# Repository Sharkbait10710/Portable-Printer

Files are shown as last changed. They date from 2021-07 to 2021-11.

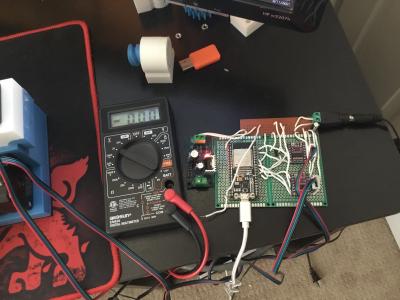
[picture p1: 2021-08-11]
Portable Printer Circuit Board.jpg

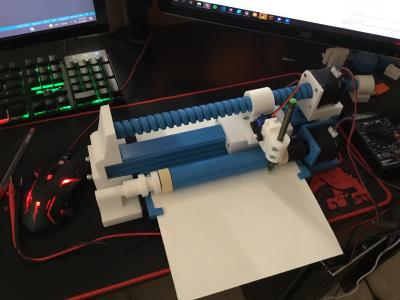
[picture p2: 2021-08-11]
Portable Printer.jpg

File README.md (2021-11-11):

# Portable Printer

The goal of this project is to create a robust printer that is lightweight and rigid in structure, capable of sketching images on 8.5 x 11 printer paper with relatively high accuracy by using a pen and resume printing capability, and has user-friendly UI software that can send virtual images to printer in real-time (image is still in progress, but would like to be drawn immediately) or by completion (image is complete and ready to print).

Access CAD design -> CAD files and open Chassis Assembly.SLDASM to view model.
All CAD, electronics, and programming were done by Dang Le.

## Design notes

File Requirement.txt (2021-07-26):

1) Structural rigid and relatively lightweight for easy transportation
    wires are simple and easy to store
    electronics are well protected and safety concealed to protect users and printer

2) Uses a pen to draw on printer paper 
    printer must be minimum 8.5 x 11 in to accomodate printer paper
    sketched drawing should be relatively accurate to user's sketched
    consistent prints
    print speed should be reasonable
    if power is lost, printer can resume printing

3) Incorporates a user-friendly UI that can accept user drawings and prints them via Portable printer
    UI should be IOS friendly 
    should be able to print real-time(image is still in progress, but would like to be drawn immediately) and by completion (image is complete and ready to print)

Possible improvements:
    as cheap as possible with maximum quality
    as fast as possible without compromising sketch quality or damage to parts
    as compact as possible

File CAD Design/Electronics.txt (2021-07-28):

Since there are two stepper motors, two DRV8255 drivers will be needed to control them
Since self-sensing is one of the capabilities of this project, the project will need two tactile sensors
        one being the endstop switch (for leadscrew motion)
        not sure if enstop would be able to detect paper though. Better than using other sensors due to price
            initially thinking of VCSEL (vertical cavity surface emitting laser), like SparkFun VL53L1X, but it
            was too expensive
        maybe use a proxmity sensor for paper sensor
        try infrared diode led IR emission and reciever
        *****USE https://www.amazon.com/Gikfun-Infrared-Emitter-Receiver-Arduino/dp/B01HGIQ8NG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
        AND https://www.youtube.com/watch?v=_mOF1JXo1DU TO CREATE OWN PROXIMITY SENSOR*****
    to detect the location of the paper and the pen
A 12V power supply is needed to power the motor drivers and a step down /  6-7 power supply is needed to
    power the ESP32 
Use PCB for circuit board
    I'm gonna try Altium CircuitMaker (software to make Gerber file) and JLCPCB (manufacturer)

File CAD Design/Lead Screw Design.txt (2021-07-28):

The lead screw cannot have a lead that is too small because the stepper motor must turn faster to make the nut carrier 
move faster. However, doing this requires sending pulses much quicker to the stepper motor, which generates more rapidly
changing currents. This in turn causes the stator windings to create stronger magnetic fields, thus more friction, and less
torque.

An increase in rotational friction due to stronger magnetic fields which are in turn due to high pulse per second (PPS) can
cause the nut mount to vibrate during prints, which would decrease print quality. Therefore, a cap on linear speed should be 
specify.

Since linear speed is equivalent to the rotational speed of the stepper motor times the lead per rotation, a larger lead 
will increase linear speed. Furthermore, lower rotational speeds are required to travel the same distance compared to leads that are 
smaller. However, this would require microstepping for more accurate positioning of the nut carrier, which would decrease the torque
output by about 30%.

Longer lead will significantly lower print time and reduce friction due to stronger magnetic fields (hence increase torque output),
but will decrease gear ratio and overall accuracy. What a short lead can due is increase precision and significantly increase torque
output, but there is a significantly trade off for speed.

So, for quick prints, longer leads are more effective, but for precise prints, short leads are better.
    for high precision, use short leads and use lower speeds.

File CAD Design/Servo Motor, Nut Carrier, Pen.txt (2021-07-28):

The nut carrier will be placed on a linear guide and is attachable by bolts and nuts. This will allow replacement of leads
which will help evaluating leads and determine which lead produces the best quality and print time.

The servo motor will be attached onto the nut carrier via bolts and nuts for easy disassemble and placed on its side
such that the shaft is pointing long at the lead screw axis. 

The servo motor will use a quick return mechanism to lift and lower the pen on the paper. A servo motor is a good choice
to do this because it provides strong output torque to prevent the pen from moving up or down, thus reducing vibrations
and improving print quality. 

The pen will be mounted on a pen mount that will securely hold the pen and prevent the pen from slipping. A pen 
coupling would be needed to do this and should be able to tighten and untighten for easy disassemble. The pen mount will
be able to move up and down and its position will be controlled via the quick return mechanism. The pen mount shouldn't 
be too heavy and should not cause the pen to lean.

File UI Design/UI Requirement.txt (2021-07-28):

requirement
    1) Should have immediate mode for user to choose
        immediate will have an idle timer that starts when user no longer drawing
        when idle timer timeouts, printer should get drawing data from user and start printing
    2) Should have complete mode for user to choose
        when user confirms that drawing is completed, printer will take the data and print out the drawing
        should have an abort option to abort drawing if user chooses to do should
    3) Should have a resume feature
        software should check if printer is still running and/or completed drawing
        if not completed, software should log the print job's progress so that when printer is online again, printing can resume
        user should be notified that printer has not finished printjob and that printer has been turned off
    4) User drawing should be logged 
    5) User should be able to draw on UI and drawing data can be exported to printer
        *ideal if UI can reduce print time as much as possible, but maximize print quality
    6) Closed boundaries in drawing should be shaded or any other method that is NOT filled in
    7) Software will notify user when drawing is completed
    8) Software is IOS compatible

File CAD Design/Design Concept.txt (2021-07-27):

Major Parts

    Chassis
        Consist of NEMA 17 stepper motor, lead screw, and nut carrier that moves pen mount
        houses electronics
        paper passes through Chassis
        *ball bearings to house lead screw
        *rod shaft to support nut carrier
        *use rectangular structure embedded under lead screw

    Pen Mount
        actached to nut carrier and moves as NEMA 17 rotates its shaft
        tightly attached to pen
        uses servo motor to lift and depress pen
        can lift pen easily and quickly
        mounted on wheels for reduction of friction
        use quick-draw (not correct name) mechanism to lift pen during non-drawing time
        sensor to help locate pen

    Roller
        accepts paper and consistent pushes paper under pen mount   
        paper distance inside chassis is consistently and accurately controlled
        controlled using spur gear and stepper motor
        feeds paper into chassism where pen will draw on paper
        should be able to push paper in and pull paper out
        sensor to detect paper

    Paper Dispenser
        straightens paper and minimizes curls in the paper
        should keep paper down as pen is moving back and forth

    electronics
        use PCB board and attach to all motors (stepper and servo), sensor, and microncontroller
        microncontroller is esp32 for internet capability
        12V power supply 
        DRV8255 motor driver
        *need 5-8ish power supply to power esp32

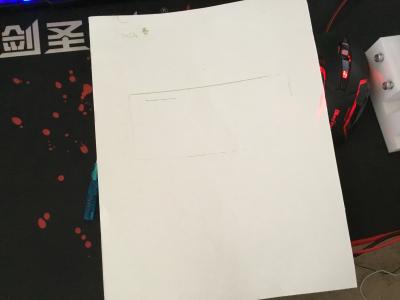
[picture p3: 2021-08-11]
Sketch of Rectangle.jpg

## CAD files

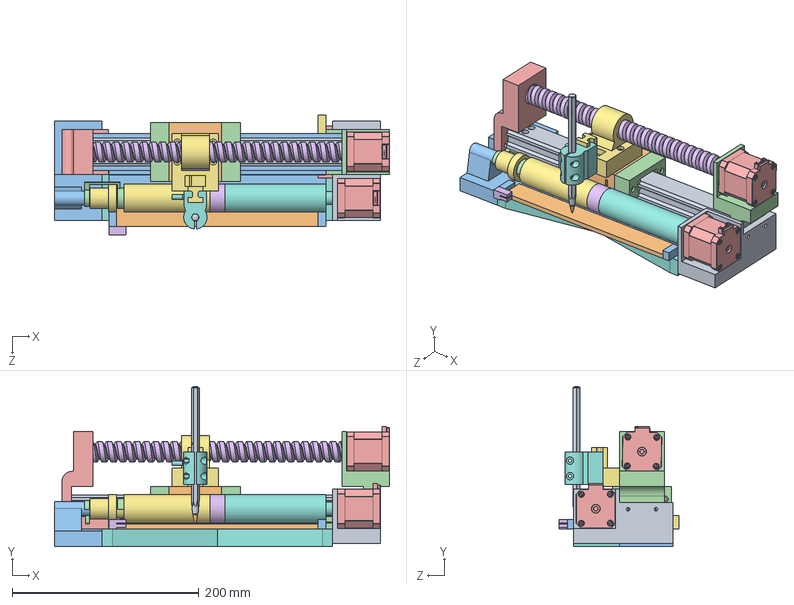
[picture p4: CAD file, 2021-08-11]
CAD Design/CAD Files/Chassis Assembly.SLDASM
358.8 x 171.4 x 128.7 mm
Linear Guide Rail
Linear Guide Carrier
7by3 inch Ball x 104
Linear Guide Cap x 2
Nema 17 Stepper Motor x 2
lead screw
nut carrier
Bic Pen Coupling
bic_pen
inner part
Chassis
chassis right wing
chassis left wing
paper feed roll
roller
roller 2
chassis right foot
paper plane
chassis left foot
paper detector
paper feed chassis part
paper side feeds
paper side back
X Brace

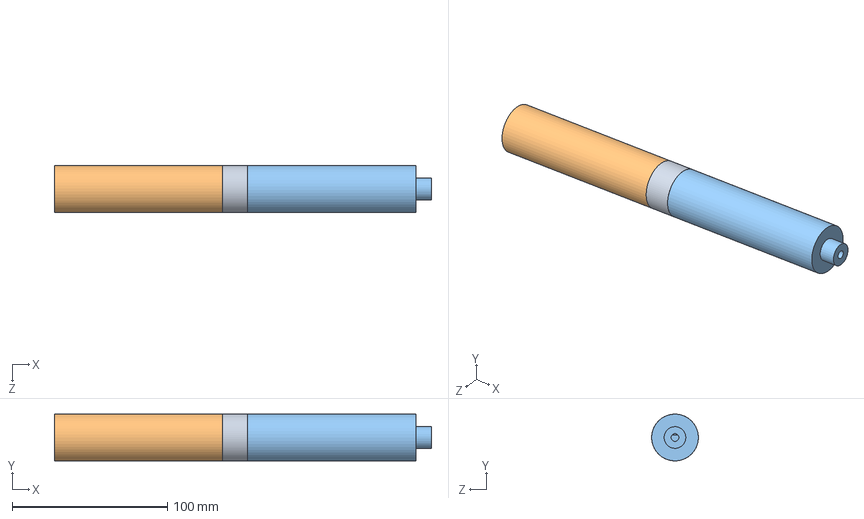
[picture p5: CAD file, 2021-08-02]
CAD Design/CAD Files/roller.SLDASM
243.0 x 30.1 x 30.2 mm
paper feed roll
roller
roller 2

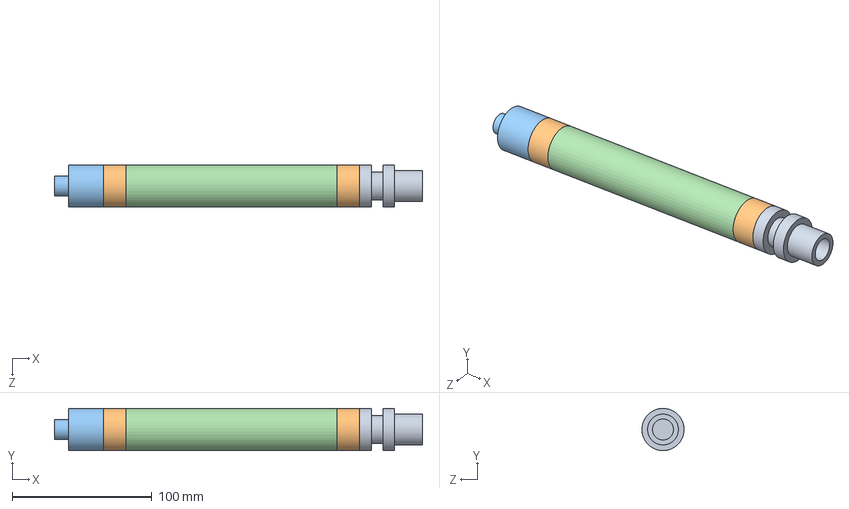
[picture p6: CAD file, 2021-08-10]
CAD Design/CAD Files/Improvements/roller improv.SLDASM
263.0 x 30.2 x 30.2 mm
roller improv
paper feed roll x 2
roller 2 improv
roller improv 3

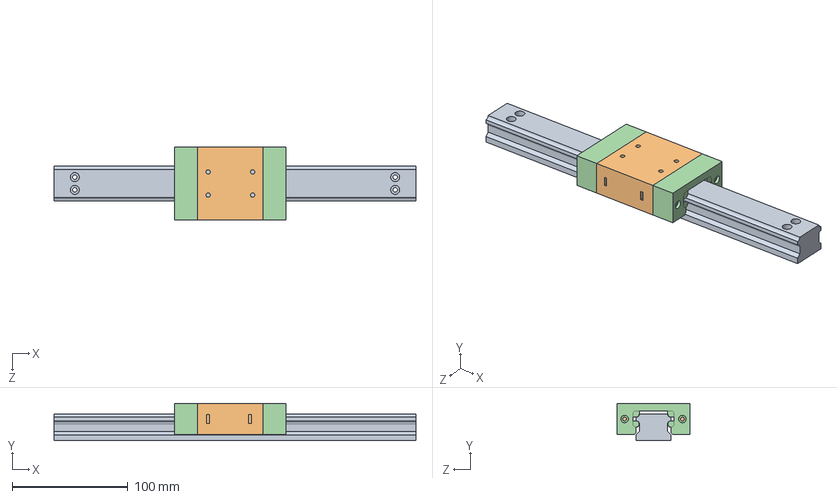
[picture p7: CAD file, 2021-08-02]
CAD Design/CAD Files/linear guide.SLDASM
313.0 x 32.1 x 63.5 mm
Linear Guide Rail
Linear Guide Carrier
7by3 inch Ball x 104
Linear Guide Cap x 2

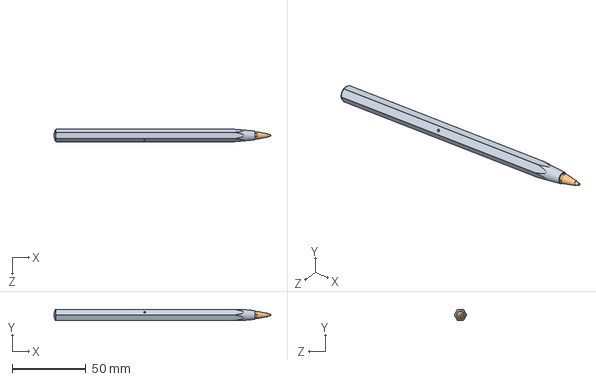
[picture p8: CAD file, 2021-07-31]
CAD Design/CAD Files/Bic Pen.SLDASM
147.1 x 7.40 x 8.50 mm
bic_pen
inner part

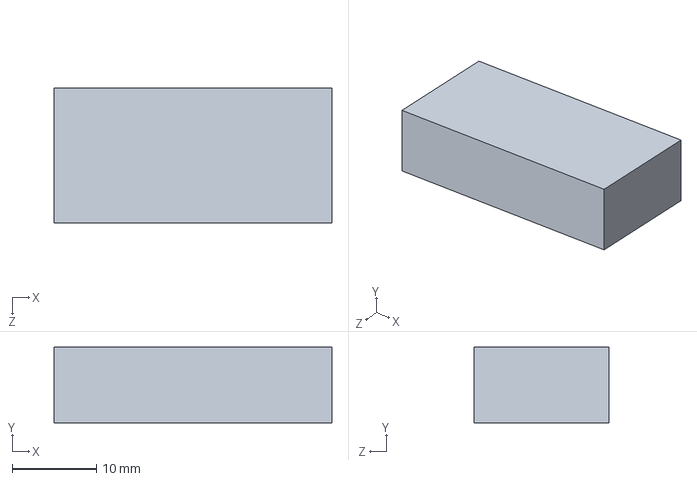
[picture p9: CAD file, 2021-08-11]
CAD Design/CAD Files/Improvements/chassis right wing support 3.SLDPRT
33.0 x 9.00 x 16.1 mm

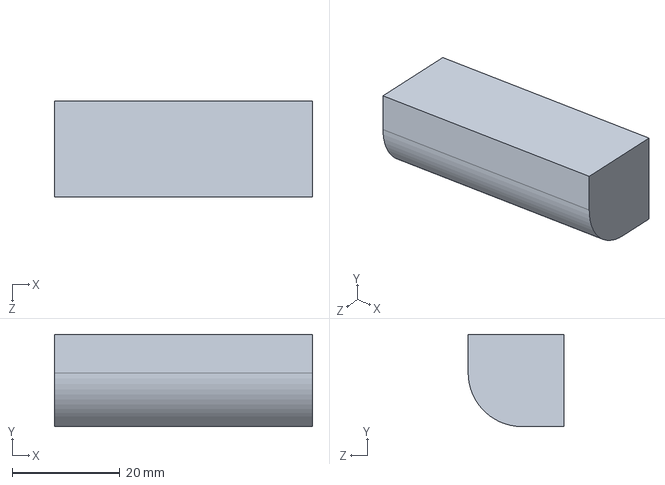
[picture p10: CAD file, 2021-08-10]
CAD Design/CAD Files/Print Folder/chassis right wing support P.SLDPRT
48.0 x 17.1 x 17.8 mm

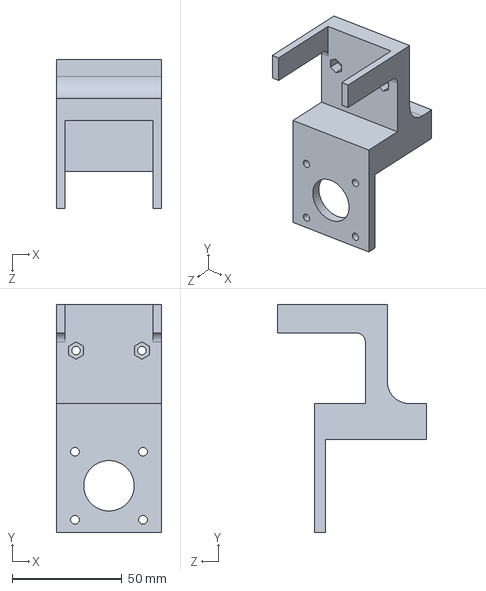
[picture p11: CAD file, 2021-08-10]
CAD Design/CAD Files/chassis right wing.SLDPRT
48.0 x 103.9 x 67.8 mm

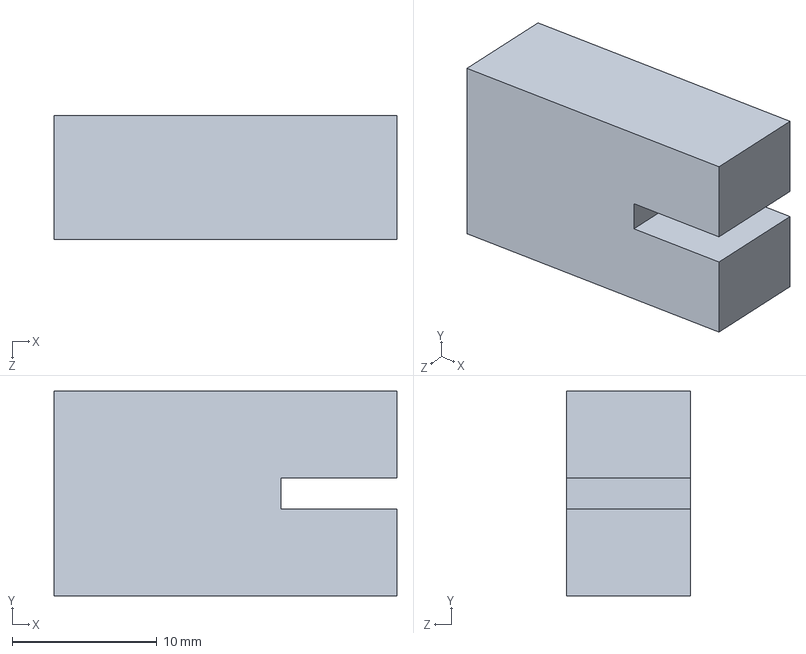
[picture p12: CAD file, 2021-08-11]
CAD Design/CAD Files/Improvements/paper side back 2.SLDPRT
23.7 x 14.2 x 8.55 mm

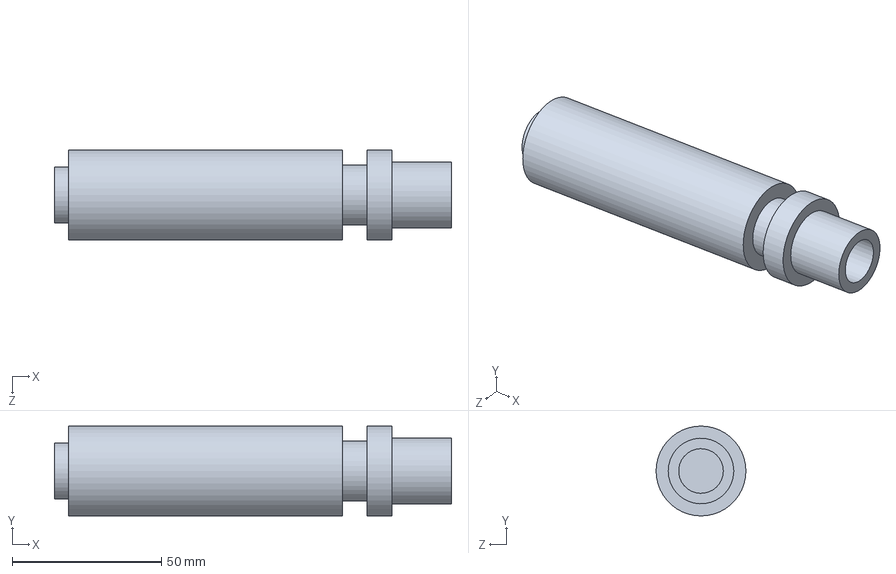
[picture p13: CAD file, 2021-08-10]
CAD Design/CAD Files/Print Folder/roller P.SLDPRT
133.2 x 30.2 x 30.2 mm

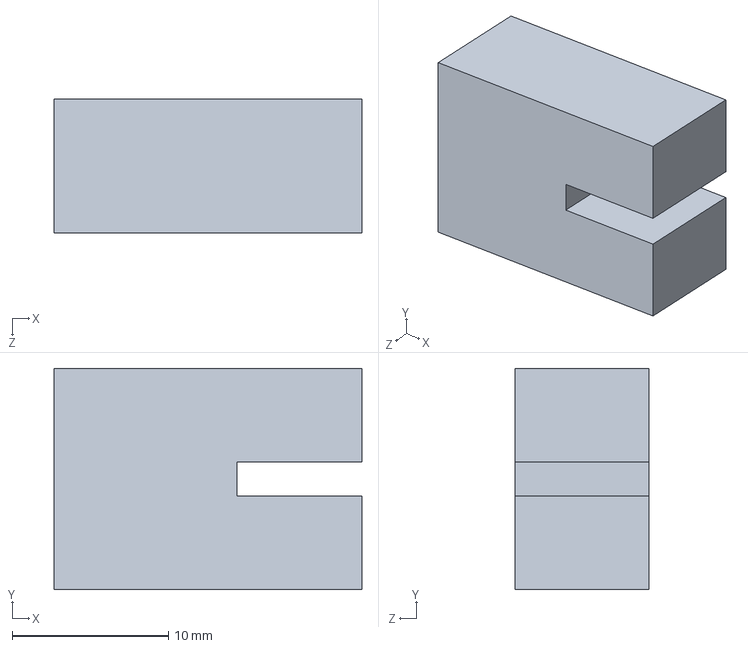
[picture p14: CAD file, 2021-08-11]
CAD Design/CAD Files/Improvements/paper side back.SLDPRT
19.7 x 14.2 x 8.55 mm

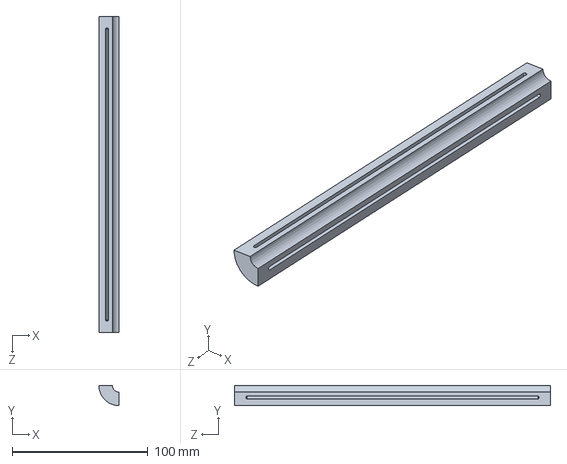
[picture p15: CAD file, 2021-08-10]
CAD Design/CAD Files/paper slide.SLDPRT
15.0 x 15.0 x 232.5 mm

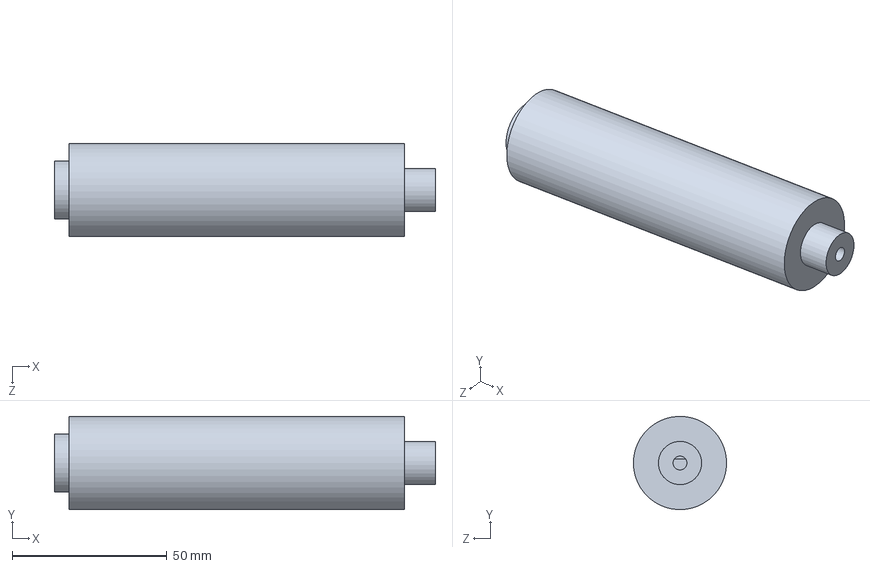
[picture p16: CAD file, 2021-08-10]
CAD Design/CAD Files/Print Folder/roller 2 P.SLDPRT
123.2 x 30.1 x 30.2 mm

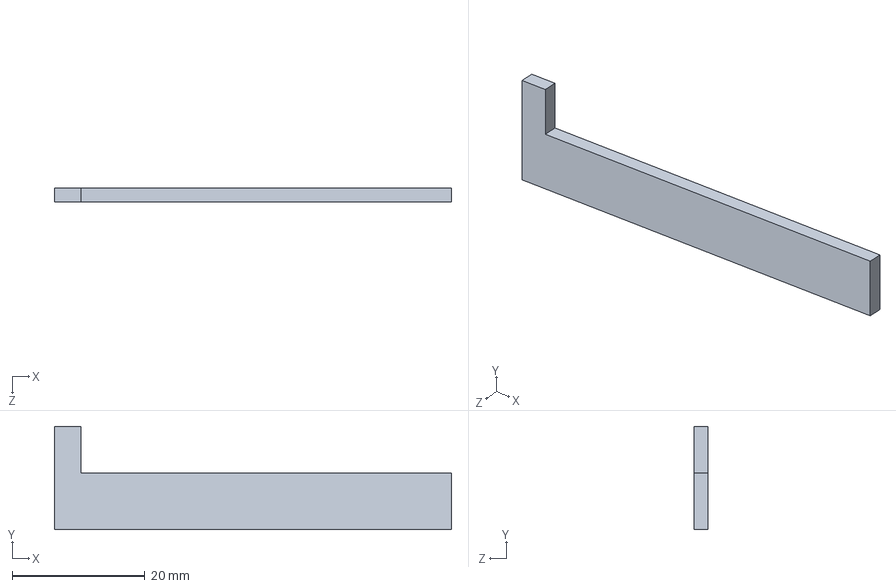
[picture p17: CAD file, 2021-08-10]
CAD Design/CAD Files/Improvements/paper feed chassis part 3.SLDPRT
59.9 x 15.5 x 2.15 mm

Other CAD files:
CAD Design/CAD Files/Print Folder/chassis right wing support 2 P.SLDPRT
CAD Design/CAD Files/Chassis.SLDPRT
CAD Design/CAD Files/Improvements/chassis right wing support 2.SLDPRT
CAD Design/CAD Files/Print Folder/Chassis P.SLDPRT
CAD Design/CAD Files/7by3 inch Ball.SLDPRT
CAD Design/CAD Files/Bic Pen Coupling.SLDPRT
CAD Design/CAD Files/Improvements/X Brace 2.SLDPRT
CAD Design/CAD Files/Improvements/X Brace.SLDPRT
CAD Design/CAD Files/Improvements/chassis left foot mod.SLDPRT
CAD Design/CAD Files/Improvements/chassis left foot no rod support.SLDPRT
CAD Design/CAD Files/Improvements/chassis left foot only rod support.SLDPRT
CAD Design/CAD Files/Improvements/chassis right wing support.SLDPRT
CAD Design/CAD Files/Improvements/paper feed chassis part 2.SLDPRT
CAD Design/CAD Files/Improvements/paper feed chassis part.SLDPRT
CAD Design/CAD Files/Improvements/paper side feeds.SLDPRT
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

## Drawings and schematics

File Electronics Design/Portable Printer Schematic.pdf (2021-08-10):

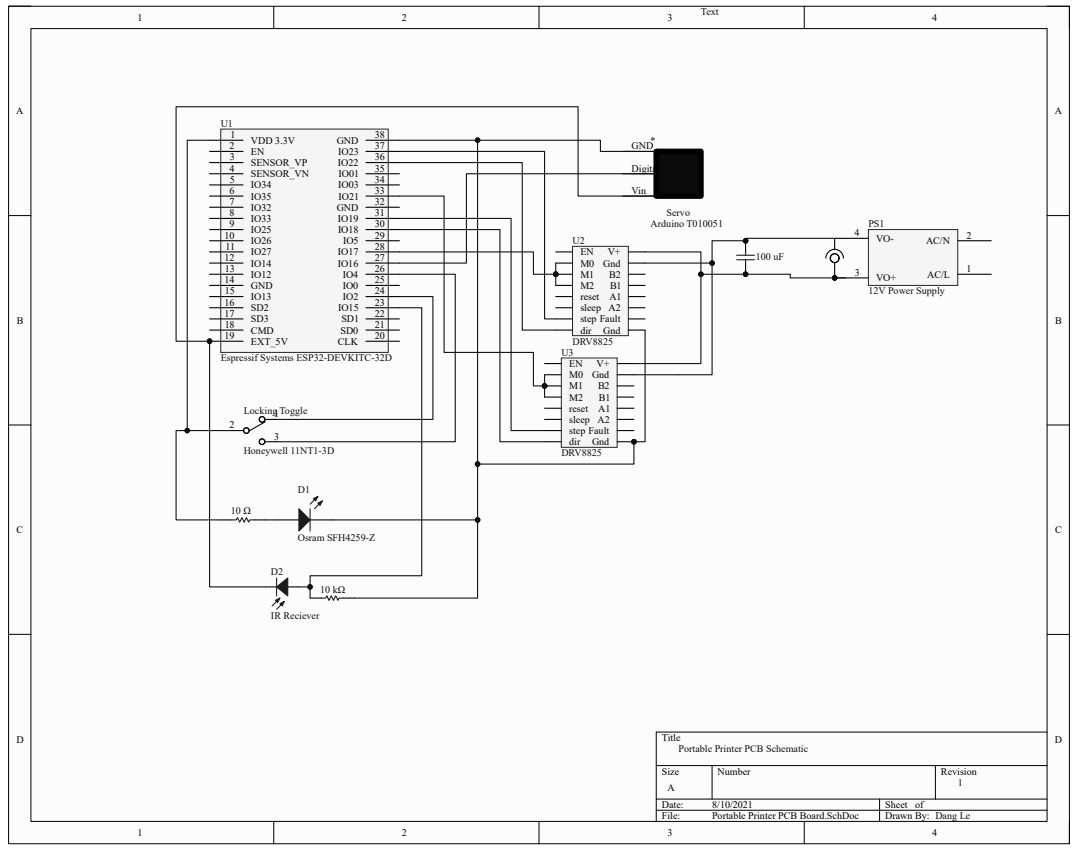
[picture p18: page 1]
VDD 3.3V 1 EN 2 SENSOR_VP 3 SENSOR_VN 4 IO34 5 IO35 6 IO32 7 IO33 8 IO25 9 IO26 10 IO27 11 IO14 12 IO12 13 GND 14 IO13 15 SD2 16 SD3 17 CMD 18; EXT_5V 19; CLK; 31 GND; 37 GND; Locking Toggle; Honeywell 11NT1-3D; Osram SFH4259-Z; GND; Digital; Vin; Servo; Arduino T010051; EN M0 M1 M2 reset sleep step dir Gnd; Fault; Gnd; DRV8825; 12V Power Supply; Text; IR Reciever

Espressif Systems ESP32-DEVKITC-32D

Title
Portable Printer PCB Schematic

Size A | Number | Revision 1

Date: 8/10/2021 | Sheet of
File: Portable Printer PCB Board.SchDoc | Drawn By: Dang Le

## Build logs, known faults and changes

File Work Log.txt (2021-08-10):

2021-07-26 13:45:13
    {
        Created Git Repository
        Laid out general idea of project in README.md
    }

2021-07-26 14:11:13
    {
        watched youtube.com/watch?v=6BkYcqe8Vmo "How to convert rotational motion into linear motion | Lemurian Designs"
            and discovered the lead screw assembly
    }

2021-07-26 14:44:10
    {
        watched https://www.youtube.com/watch?v=BstZUC4tcOA "Power Screws - Torque to Force Relationships in Just Over 10 Minutes!"
            and learned that one full rotation, for single thread screw, will advance output load by lead (l)
    }

2021-07-26 15:00:18
    {
        Wrote requirement for project
    }

2021-07-26 15:12:06
    {
        Created Design folder, which would house the SW files, and currently contains the general design idea text file
    }

2021-07-27 07:35:52 
    {
        Continued working on Design Concept. Have good idea of CAD design now
    }

2021-07-27 07:45:39
    {
        Laid out requirement for UI
    }

2021-07-27 17:02:59 
    {
        Researched GUI design and how to use CSS. Found Bootstrap and plan to implement it.
        Learned about Ultralight which "enables you to build your application's GUI with web pages and C/C++"
    }

2021-07-27 19:19:34
    {
        Learned about linear guide from https://youtu.be/XZXadrjIm_4 and discovered cad file at https://www.thingiverse.com/thing:2847294
    }

2021-07-27 19:59:05
    {
        Instead of using shafts for linear bearings, using linear guide is better since it saves more space. The thingiverse link would
        serve as a guide. Need balls though, this link looks good https://www.amazon.com/500Pcs-Assorted-Loose-Bicycle-Bearing/dp/B085T3BT92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
    }

2021-07-28 06:20:56 
    {
        Learned how stepper motors work from https://www.youtube.com/watch?v=TWMai3oirnM "Stepper Motor - How It Works." 
        Pulses are sent to stepper motor which create varying magnetic fields to turn a permanent magnet (or something similar) to in order to change its rotational position.
    }

2021-07-28 06:37:45
    {
        Learned even more about stepper motor. A single digital pulse moves a single step by energizing coil (I think running current briefly generates a magnetic field in 
        one coil, but when current begins to stop a magnetic field in the opposite direction is generated). Microstepping is also possible.
    }

2021-07-28 06:44:43
    {
        I learned more about stepper motors and learned that there are 2 coils inside a stepper motor and each coil is energized alternatively in order to generate
        magnetic fields in the same direction to rotate the shaft.
        Check out https://www.youtube.com/watch?v=09Mpkjcr0bo "How Stepper Motors Work - Electric motor"
    }

2021-07-28 07:19:03
    {
        I worked on the lead screw design. I will wait for the paper feed roller design after I recieve the rollers today. I'm not completely sure how the roller will
        effective feed paper without causing curlings. I'm also not sure how to prevent the paper from curling in general as it enters the chassis. My questions are 
        "Does the pen cause the paper to curl?" "Will the paper need to be fed into a narrow slit to hold the paper down and will the slit cause the paper to curl?"
    }

2021-07-28 07:44:36 
    {
        Worked on the Servo Motor, Nut Carrier, and Pen design. 
    }

2021-07-28 10:38:52
    {
        Have a much better idea as to what to do. Know what sensors to use to calibrate roller and pen. Know where to buy sensor. Have a good idea on what electrical
        components to use. I think now is a good time to start designing
    }

2021-07-28 17:39:00
    {
        Worked on linear guide. Got into some trouble.
        Issues were: balls are same size as holes, but for some reason, there is interference, even for cylinder holes (which should be an obvious fit)
                        difficulty assembling all the parts. Not sure why there are interference when I tried to fit the 15 balls between the carrier / cap 
                        and rail
        Slightly larger holes might be good because lubrication 
    }

2021-07-29 09:00:10
    {
        Linear Guide assembly is complete, but assembling 6-32 screws and nuts is too difficult for me right now. Going to start working on the lead screw and nut carrier.
    }

2021-07-29 10:24:58
    {
        Learned how to draw threads. Just finished lead screw.
    }

2021-07-29 14:24:55
    {
        Worked on nut carrier (servo mount), but seems like the linear guide is a bit big. Could be improved. Check nut holes on linear guide carrier. Perhaps walls should be 
        thickened. 
    }

2021-07-29 15:01:40
    {
        Continued to develop the servo mount on the nut carrier, but will attempt to print to evaluate quality
    }

2021-07-29 19:54:06
    {
        Tried setting up Ultralight, but not working. Probably better to use something different to develop UI
    }

2021-07-31 18:43:48
    {
        Printed out rail, pen mount, and linear guide. Quality of all are not up to standard. Rough surfaces for those rail (by Longer) and parts printed on Labist (pen mount)
        have very bad tolerance. This implies that labist produces worst quality parts than Longer and adjustments must be made.
    }

2021-08-02 10:11:35
    {
        Working on roll. Just finished with chassis assembly
    }

2021-08-02 13:02:19
    {
        Just finished mechanical aspects of portable printer.
    }

2021-08-03 07:55:22
    {
        Today will be mainly focused on printing out parts and waiting.
    }

2021-08-04 13:00:07
    {
        Completed Schematic
    }

2021-08-10 08:45:40
    {
        A whole week of printing and seems like theres nearly satisfactory precision in the roller. A lot of improvment parts. Going to work on GUI. 
    }

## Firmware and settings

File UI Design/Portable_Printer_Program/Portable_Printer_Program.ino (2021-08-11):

#include "Websocket.h"
#include "Stepper.h"
#include "Servo.h"
//Access the WSMsg variable to evalute what message is being returned from WS server

//Variables
unsigned motor_1_retuns = 0;
unsigned motor_2_retuns = 0;
int servo_pos = 50;
//Task for multithreading
TaskHandle_t motorTask;

void setup() {
  WSSetup("BadWifi", "Sanmina02", "192.168.0.28", 8082);
  stepperSetup();
  servoSetup();
  servo.write(map(servo_pos, 0, 100, 0, 180));

  xTaskCreatePinnedToCore(
                    motorTaskcode,   // Function to implement the task
                    "motorTask", // Name of the task 
                    10000,      // Stack size in words 
                    NULL,       // Task input parameter 
                    0,          // Priority of the task 
                    NULL,       // Task handle. 
                    0);  // Core where the task should run 
}

void evaluateWSMsg(String& str) {
  if (str.indexOf("Turn stepper 1 OFF") > -1) {
    USE_SERIAL.println("Turn stepper 1 OFF Continuously");
    motor_1_retuns = 0;
  }
  else if (str.indexOf("Turn stepper 1 CC") > -1) {
    USE_SERIAL.println("Turn stepper 1 CC Continuously");
    motor_1_retuns = 1;
  }
  else if (str.indexOf("Turn stepper 1 C") > -1) {
    USE_SERIAL.println("Turn stepper 1 C Continuously");
    motor_1_retuns = 2;
  }
  if (str.indexOf("Turn stepper 2 OFF") > -1) {
    USE_SERIAL.println("Turn stepper 2 OFF Continuously");
    motor_2_retuns = 0;
  }
  else if (str.indexOf("Turn stepper 2 CC") > -1) {
    USE_SERIAL.println("Turn stepper 2 CC Continuously");
    motor_2_retuns = 1;
  }
  else if (str.indexOf("Turn stepper 2 C") > -1) {
    USE_SERIAL.println("Turn stepper 2 C Continuously");
    motor_2_retuns = 2;
  }
  else if (str.indexOf("Adjust servo to ") > -1) {
    servo_pos = str.substring(16,str.length()).toInt();
    USE_SERIAL.println("Adjust servo to " + str.substring(16,str.length()));
  }

  str = "";
}

void MotorAction() {
  switch (motor_1_retuns) {
    case 0: 
      break;
    case 1: {USE_SERIAL.println("Step1CC"); stepper_1.move(MOTOR_STEPS*MICROSTEPS);}
      break;
    case 2: {USE_SERIAL.println("Step1C"); stepper_1.move(-MOTOR_STEPS*MICROSTEPS);}
      break;
  }

  switch (motor_2_retuns) {
    case 0:
      break;
    case 1: {USE_SERIAL.println("Step2CC"); stepper_2.move(MOTOR_STEPS*MICROSTEPS);}
      break;
    case 2: {USE_SERIAL.println("Step2C"); stepper_2.move(-MOTOR_STEPS*MICROSTEPS);}
      break;
  }

  if (servo.read() != map(servo_pos, 0, 100, 0, 180)) {
    USE_SERIAL.println("Moving to " + String(map(servo_pos, 0, 100, 0, 180)));
    servo.write(map(servo_pos, 0, 100, 0, 180));
  }
}

void motorTaskcode( void * pvParameters ){
  Serial.print("Task1 running on core ");
  Serial.println(xPortGetCoreID());

  for(;;){MotorAction(); delay(10);}
}

void loop() {
  //Constantly evaluate WS connection for messages 
  webSocket.loop();
  evaluateWSMsg(WSMsg);
}

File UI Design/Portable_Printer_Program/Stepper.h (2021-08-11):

#ifndef STEPPER_H
#define STEPPER_H

//Libraries
#include <Arduino.h>
#include "DRV8825.h"

//Defining DRV8825 pins for Stepper 1 (lead screw)
#define Stepper_1_M0 17
#define Stepper_1_step 19
#define Stepper_1_dir 18

//Defining DRV7725 pinsfor Stepper 2 (roller)
#define Stepper_2_M0 2
#define Stepper_2_step 23
#define Stepper_2_dir 22

// Acceleration and deceleration values are always in FULL steps / s^2
#define MOTOR_ACCEL 2000
#define MOTOR_DECEL 1000
#define MOTOR_STEPS 200   //6400 steps for microstepping
#define RPM 120           //Revolutions per minute
#define MICROSTEPS 1      //Set to 16 for microstep

//Create DRV8825 stepper objects
DRV8825 stepper_1(MOTOR_STEPS, Stepper_1_dir, Stepper_1_step, 
        Stepper_1_M0, Stepper_1_M0, Stepper_1_M0);
DRV8825 stepper_2(MOTOR_STEPS, Stepper_2_dir, Stepper_2_step, 
        Stepper_2_M0, Stepper_2_M0, Stepper_2_M0);

void stepperSetup() {
  stepper_1.begin(RPM, MICROSTEPS);
  stepper_2.begin(RPM, MICROSTEPS);
  digitalWrite(Stepper_1_M0, HIGH);
  digitalWrite(Stepper_2_M0, HIGH);
  //Energizes coil to hold motor shaft (disable to release hold)
  stepper_1.enable();
  stepper_2.enable();
  
  stepper_1.setSpeedProfile(stepper_1.LINEAR_SPEED, MOTOR_ACCEL, MOTOR_DECEL);
  stepper_2.setSpeedProfile(stepper_2.LINEAR_SPEED, MOTOR_ACCEL, MOTOR_DECEL);
} //Use stepper.move(-MOTOR_STEPS*MICROSTEPS) to take motor step
#endif

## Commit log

2021-07-26 Created README
    A general requirement for the Portable Printer Project
2021-07-27 Added New Files
    Chassis and Nema Files
    [Chassis.SLDPRT, Nema 17 Stepper Motor.SLDPRT]
2021-07-27 Added More to Design Concept
    Have good idea of CAD design
    Aiming to work on UI today
    [Chassis.SLDPRT, Nema 17 Stepper Motor.SLDPRT]
2021-07-28 Learned about which linear bearing to use
    Using linear guide will save a lot more space than rod shafts, but needs balls
2021-07-28 Learned more about stepper motor and started writing out designs for lead screw, pen carrier, and servo motor
2021-07-28 Re organized Files
    [Towerpro Micro Servo 9g.SLDPRT]
2021-07-29 Worked on linear guide, there were errors
    See Issues were: balls are same size as holes, but for some reason, there is interference, even for cylinder holes (which should be an obvious fit)
    difficulty assembling all the parts. Not sure why there are interference when I tried to fit the 15 balls between the carrier / cap
    and rail. See work log 2021-07-28 17:39:00
    [7by3 inch Ball.SLDPRT, Linear Guide Cap.SLDPRT, Linear Guide Carrier.SLDPRT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]
2021-07-29 Finished Linear Guide Assembly and Just finished Lead Screw
    Having troubling assembling 6-32 screws and nuts
    [Linear Guide Cap.SLDPRT, Linear Guide Carrier.SLDPRT, Nema 17 Stepper Motor.SLDPRT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]
2021-07-30 Did some research on UltraLight and printing out nut carrier
    UltraLight not cooperating very well, has error MSB3073, and not sure if nut carrier can be printed in decent quality
    [Linear Guide Carrier.SLDPRT, Towerpro Micro Servo 9g.SLDPRT, lead screw assembly.SLDASM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]
2021-07-31 Adjusted Nut Carrier
    Now can accommodate pen coupling
    [nut carrier.SLDPRT]
2021-07-31 Added Bic Pen
    [Bic Pen Coupling.SLDPRT, bic_pen.SLDPRT, inner part.SLDPRT]
2021-07-31 Added BIC Pen coupling
    [Bic Pen Coupling.SLDPRT, Bic Pen.SLDASM, bic_pen.SLDPRT]
2021-07-31 Adjusted Coupling and Carrier
    [Bic Pen Coupling.SLDPRT, lead screw assembly.SLDASM, nut carrier.SLDPRT]
2021-07-31 Added Pen mount, quick mechanism, and chassis. Printed linear and pen mount out
    Printed parts have some defects. Holes are smaller than expected. The lienar rail printed off the plate
    [Bic Pen.SLDASM, Chassis Assembly.SLDASM, Chassis.SLDPRT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]
2021-08-02 Completed Chassis, lengthen lead screw, and begin working on roller
    [Bic Pen Coupling.SLDPRT, Chassis Assembly.SLDASM, Chassis.SLDPRT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]
2021-08-02 Completed roller and completed mechanical aspect of portable printer
    [Bic Pen Coupling.SLDPRT, Chassis Assembly.SLDASM, Chassis.SLDPRT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]
2021-08-02 Added paper slide to help user guide paper into printer
    [Chassis Assembly.SLDASM, Chassis.SLDPRT, paper slide.SLDPRT]
2021-08-03 Made Adjustments to some parts and introduced a print folder to contain adjusted parts that will be printed
    [Chassis Assembly.SLDASM, Chassis P.SLDPRT, Chassis.SLDPRT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]
2021-08-04 Minor Adjustments to holes
    [Bic Pen Coupling P.SLDPRT, nut carrier 2 P.SLDPRT, nut carrier 3.SLDPRT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]
2021-08-04 Adjusted chassis wings / feet for printing and completed schematic
    [chassis left foot P.SLDPRT, chassis left wing P.SLDPRT, chassis right foot P.SLDPRT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]
2021-08-10 Added electronics schematic
2021-08-10 Improvement Folder
    [X Brace 2.SLDPRT, X Brace.SLDPRT, chassis left foot mod.SLDPRT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]
2021-08-10 Print Folder
    [chassis left foot P.SLDPRT, chassis left wing P.SLDPRT, chassis right foot P.SLDPRT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]
2021-08-11 Added GUI Server
    Setup websocket server with ESP32. GUI can now communicate consistently with ESP32 by sending strings.
    [Chassis Assembly.SLDASM, paper side back 2.SLDPRT, paper side back.SLDPRT]
2021-08-11 Added Servo, Stepper, and Improved WebSocket
2021-08-11 Project Complete!
    [chassis right wing support 3.SLDPRT]
